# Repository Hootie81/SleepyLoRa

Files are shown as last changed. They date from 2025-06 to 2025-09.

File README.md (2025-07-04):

# SleepyLora Blinds System

A low-power wireless smart blinds system using LoRa to enable low power yet fast response to commands - 100% local control.

In July 2023 I set out the key requirements for the project
- 100% local control - no 3rd party servers etc.
- solar powered with up to 3days bad weather.
- back driveable without breaking.
- secure
- be cheap

This system is 100% local, no external access required at all.

A 2.5w 380mm x 70mm thin film flexible panel is enough to keep a 2000mah battery fully charged with less than 2 hours a day of sun. the 2000mah battery lasts about 10 days with no panel connected.

Key design requirement was for the blinds to still operate by hand, so a mechanism was developed that disengages the motor from the actuator once the move command is complete. [See disengage mechanism video](https://youtu.be/guv8YasCPMQ?si=FenjIrAAZN0NFrJr)

Position is sensed using a linear potentiometer thats connected to the actualing arm, so the blinds always know their position.

The actuators now use a PID controller to target a specified time for each move, this allows the motor to run significantly quieter and allows syncronsation of blinds with different operating forces/friction. All PID, PWM and timing settings are customisable.

All data packets are AES128 encrypted and hardened against replay attacks using 1 second interval TOTP, so no-one can open your blinds but you.
Costs are kept low by using cheap modules form china, assembled onto custom PCB's and housed in 3d printed parts.
The wired slaves are powered by the master, thus only a single battery and solar panel per system and a significant reduction in actuator cost too. 

This project includes electronics designs, firmware, and 3D printable parts for a complete DIY solution.

- [3D Parts Assembly Video](https://youtu.be/qfTnw-1N8DM?si=_8NIrLeuZx0titTB)
- [Electronics Assembly Video](https://youtu.be/dtDF-GL67Ew?si=iw6Ndi3xGu8mUtQ1)

This has been a couple of years in the making, and still very much a work in progress. If you find this project useful, please consider supporting my work:



Your support helps me keep building and maintaining open-source projects like this. Thank you!

---

### System

- **Gateway**:  
  Heltec Wireless Stick Lite V3, Connects to WiFi and MQTT, relays commands between Home Assistant and LoRa network. 
  Exposes a web portal for configuration and security key generation

- **Master**:  
  Blind actuator with a Heltec Wireless Stick Lite V3, voltage booster, motor driver, position sensor and RS485 module.
  Powered from a single cell lipo battery or USB.
  Can supply power to and control multiple slave devices via RS485.
  Exposes a web portal for configuration and firmware updates. (via button press or mqtt command)

- **Slave**:  
  Blind actuator with an ESP32-c3 module, motor driver, position sensor and RS485 module. 
  Powered by the Master
  Exposes a web portal for address configuration and OTA updates. (via button press or mqtt command)
  Connects to the master using a flat 6core telephone cable terminated with 4pin JST XH2.54 connectors
  
---

## Features

- **Long-range LoRa wireless communication**
- **Easy WiFi and MQTT Setup**
- **Easy key generation and sharing**
- **Home Assistant auto-discovery**
- **OTA firmware updates**
- **Configurable RS485 slave addressing**
- **Easy Open/Closed position setting via web portal**
- **PWM speed control with PID controller for quiet operation**
- **Auto calibration feature for disengage mechanism**
- **Low-power operation** 
- **3D-printable hardware** 
- **Easy to assemble electronics**
- **Open-source** 

---

## Project Structure

- **3d_prints/**  
  STL files for all mechanical parts 

- **Electronics/**  
  KiCad schematics, PCB layouts, and Gerber files for the master and slave boards.

- **SleepyLoraGateway/**  
  Firmware for the LoRa gateway device. Handles MQTT, Home Assistant integration, and LoRa communication. 

- **SleepyLoraMaster/**  
  Firmware for the master device, an actuator for one set of shutters, with the capability to power and control several slave devices via RS485.

- **SleepyLoraSlave/**  
  Firmware for the slave device, an actuator for one set of shutters and reports position/status.

---

## Getting Started

- Order all the parts/modules from Aliexpress, list in `Electronics/`
- Order PCB/s using the KiCad files in `Electronics/`
- Print and assemble the required parts from `3d_prints/`
- Solder the modules onto the PCB's
- Install electronics in 3d printed base
- Flash the appropriate firmware to each device:
  - Gateway: `SleepyLoraGateway/`
  - Master: `SleepyLoraMaster/`
  - Slave: `SleepyLoraSlave/`
- Configure the Gateway
  - Connect to the SleepyLoraGateway AP (pw: blind1234)
  - Set the WiFi, MQTT and NTP server information.
  - Set LoRa Region
  - Generate keys and download them. 
  - Save and reboot.
  - Gateway Connects to WiFi, MQTT and Sync's its time.
  - Gateway Publishes gateway metric discovery info and publishes data.
- Configure the Master/s
  - Connect to the SleeplyLoRaMaster AP (pw: blind1234)
  - Load the keys file downloaded above
  - Set Open and Closed limits
  - Save and reboot
  - Master sync's time with gateway
  - Master transmits Device metrics and status to Gateway.
  - Gateway publishes Blind discovery info, subscribes to MQTT topics, and publishes data every 60sec.
  - Master will transmit device metrics and status every minute.
- Check your HA MQTT integration, the Gatway, device and blind will magically appear after a minute or so. 
- Optionally - configure the slave/save
  - Connect the slave to the master 
  - Press the reset button on the master
  - Master will scan for slaves on initial bootup
  - Master transmits slave status to Gateway.
  - Gateway publishes Blind discovery info, subscribes to MQTT topics, and publishes data every 60sec.
  - Open web portal via MQTT or from the master web portal
  - Set Open and Closed limits
  - Master will poll slave and transmit status every minute.
  - Optionally - if a second slave is required
    - press the "Open Web Portal" button on the slave device in HomeAssistant
	- Connect to the SleeplyLoRaSlave AP (pw: blind1234)
	- Change the slave number
	- Save to flash
    - Scan for slaves via the master's web portal (Or press the reset button on the master)
    - Master will rescan for slaves

---

## Documentation

- Each firmware folder contains its own README with build and usage instructions.
- For wiring, assembly, and setup, see my videos on youtube or open an issue for help.

---

## ToDo

- Update slave firmware to use new motor controller library and updated web portal.
- Add feature to get/set all blind settings via MQTT.
- Design an enclosure to the battery and charger modules.
- Make an injection moulding option for the plastic parts.

---

## License

This project is open-source under the MIT License.  
See [LICENSE](LICENSE) for details.

---

## Credits

- Hardware, firmware, and 3D design by Chris Huitema
- Built with [PlatformIO](https://platformio.org/), [KiCad](https://kicad.org/), and [ESPAsyncWebServer](https://github.com/me-no-dev/ESPAsyncWebServer)

---

**Happy hacking and smart shading!**

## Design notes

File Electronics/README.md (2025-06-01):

# Electronics Folder — SleepyLoRa Project

This folder contains all the electronics design files, schematics, PCB layouts, and bills of materials (BOM) for the SleepyLoRa Blinds System. The electronics are designed to be easy to assemble, cost-effective, and reliable for DIY smart blinds control.

## Structure
- **bom.csv** — Common components and extras used across all devices (master, slave, gateway, etc.).
- **Master/** — Schematics, PCB layout, and device-specific BOM for the SleepyLoRaMaster (blind actuator/master controller).
- **Slave/** — Schematics, PCB layout, and device-specific BOM for the SleepyLoRaSlave (slave blind actuator).

Each device folder contains:
- KiCad project files (`.pro`, `.sch`, `.kicad_pcb`, etc.)
- Gerber files for PCB manufacturing
- Device-specific BOM (bill of materials)

## How to Use
1. Review `bom.csv` for the list of common components and extras needed for all devices.
2. For each device (Master, Slave, Gateway):
   - Open the corresponding folder for full schematics, PCB layout, and device-specific BOM.
   - Use the KiCad files to view or modify the design.
   - Use the Gerber files to order PCBs from your preferred manufacturer.
   - Use the device-specific BOM to order parts for that device.
3. Assemble the PCBs according to the schematics and BOMs.

## Notes
- All designs are open-source and provided as-is for DIY use.
- If you make improvements or modifications, please consider contributing back to the project!

## License
SPDX-License-Identifier: MIT

---
For questions or support, open an issue on the main [SleepyLoRa GitHub repository](https://github.com/Hootie81/SleepyLoRa).

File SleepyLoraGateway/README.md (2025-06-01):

# SleepyLoraGateway

SleepyLoraGateway is the gateway firmware for the SleepyLora Blinds System. It acts as a bridge between the local LoRa network of blind actuators and your home automation system (such as Home Assistant) via WiFi and MQTT. The gateway provides secure, local, and reliable communication for smart blind control.

## Features
- Connects to WiFi and MQTT broker for integration with Home Assistant
- Relays commands and status between Home Assistant and LoRa network
- Exposes a web portal for configuration and security key generation
- Handles LoRa communication with master devices
- AES128 encrypted packets with replay protection
- 100% local control, no third-party servers required

## Project Structure
- `src/` — Main source code for the gateway
- `include/` — Shared headers and protocol definitions (e.g., Command_Register.h)
- `lib/` — External and custom libraries
- `platformio.ini` — PlatformIO project configuration

## Getting Started
1. Clone this repository or copy the project to your PlatformIO workspace.
2. Open with VS Code and PlatformIO extension.
3. Connect your gateway hardware (e.g., Heltec Wireless Stick Lite V3).
4. Configure WiFi, MQTT, and LoRa region in the web portal after flashing.
5. Build and upload the firmware using PlatformIO.

## Configuration & Usage
- After flashing, connect to the "SleepyLoraGateway" WiFi AP (password: blind1234).
- Access the web portal to set up WiFi, MQTT, NTP, and LoRa region.
- Generate and download security keys for the system.
- Save and reboot the gateway to connect it to your home network and MQTT broker.
- The gateway will automatically publish device and blind discovery info for Home Assistant.

## Communication Protocol
- **LoRa**: Communicates with master devices using encrypted packets.
- **WiFi/MQTT**: Integrates with Home Assistant and other automation systems.
- **Command Structure**: See `include/Command_Register.h` for command codes and protocol details.

## License
SPDX-License-Identifier: MIT

Copyright (c) 2025 Chris Huitema

---
For more information, see the source code and comments in `src/main.cpp` and related files.

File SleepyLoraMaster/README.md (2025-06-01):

# SleepyLoRaMaster

SleepyLoRaMaster is the firmware for the Master actuator device
  The Master actuator device is a plantation shutter blind actuator with a 
  Heltec Wireless Stick Lite V3, voltage booster, motor driver, position sensor and RS485 module.
  Powered from a single cell lipo battery or USB.
  Can supply power to and control multiple slave devices via RS485.
  Exposes a web portal for configuration and firmware updates. (via button press or mqtt command)

## Project Structure
- `src/` — Main source code for the master controller
- `include/` — Shared headers and protocol definitions (e.g., Command_Register.h)
- `lib/` — External and custom libraries
- `platformio.ini` — PlatformIO project configuration

## Getting Started
1. Clone this repository or copy the project to your PlatformIO workspace.
2. Open with VS Code and PlatformIO extension.
3. Connect your master controller hardware (e.g., ESP32 or compatible MCU).
4. Configure any hardware-specific settings in `platformio.ini` or source files as needed.
5. Build and upload the firmware using PlatformIO.

## Communication Protocol
- **RS485 UART**: Used to communicate with slave devices. Each slave has a unique address.
- **LoRa**: Used for long-range wireless communication with a gateway using a custom encrypted protocol.

## License
SPDX-License-Identifier: MIT

Copyright (c) 2025 Chris Huitema

---
For more information, see the source code and comments in `src/main.cpp` and related files.

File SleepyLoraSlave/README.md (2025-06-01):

# SleepyLoraSlave

SleepyLoraSlave is the firmware for the slave blind actuator in the SleepyLora Blinds System. It receives commands from the master controller via RS485 UART, controls a blind motor, and reports its position and state back to the master. The slave can be configured and updated via a built-in web portal.

## Features
- Receives commands from the master controller over RS485 UART
- Controls a blind motor and reports position/state
- Web portal for configuration (slave address, etc.)
- OTA firmware updates via web portal
- Powered by the master device
- Low-power operation

## Project Structure
- `src/` — Main source code for the slave controller
- `include/` — Shared headers and protocol definitions
- `lib/` — External and custom libraries
- `platformio.ini` — PlatformIO project configuration

## Getting Started
1. Clone this repository or copy the project to your PlatformIO workspace.
2. Open with VS Code and PlatformIO extension.
3. Connect your slave hardware (e.g., ESP32-C3 or compatible MCU).
4. Configure any hardware-specific settings in `platformio.ini` or source files as needed.
5. Build and upload the firmware using PlatformIO.

## Configuration & Usage
- Connect the slave to the master using a flat 6-core telephone cable (terminated with 4-pin JST XH2.54 connectors).
- To configure the slave address or update firmware:
  - Press the button to activate the web portal.
  - Connect to the "SleepyLoRaSlave" WiFi AP (password: blind1234).
  - Access the configuration page to set the slave number or upload new firmware.

## Communication Protocol
- **RS485 UART**: Used to communicate with the master device. Each slave has a unique address.
- **Command Structure**: See `include/Command_Register.h` for command codes and protocol details.

## License
SPDX-License-Identifier: MIT

Copyright (c) 2025 Chris Huitema

---
For more information, see the source code and comments in `src/main.cpp` and related files.

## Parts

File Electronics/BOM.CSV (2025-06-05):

Part No | qty | link | notes
GA12-N20 DC 3V 6V 12V Micro Metal Gear Motor Gear Wheel Gear Motor 30RPM | 1 | https://www.aliexpress.com/item/1005005699205905.html | 3v 30rpm version
Metal Dowel Pins Stainless Steel M1 x 10mm Cylindrical Pin Locating Dowel Parallel Pins Solid Rod | 2 | https://www.aliexpress.com/item/1005005478162210.html | M1 x 10
Metal Dowel Pins Stainless Steel M2 x 20mm Cylindrical Pin Locating Dowel Parallel Pins Solid Rod | 2 | https://www.aliexpress.com/item/1005005478162210.html | M2 x 20
Hexagon Hex Socket Countersunk Flat Head Screw M3 x 6mm DIN7991 304 Stainless Steel | 2 | https://www.aliexpress.com/item/1005006180128211.html | M3 x 6
M2 Micro Carbon Steel Cross Phillips Flat Countersunk Self Tapping Screw Machine Laptop Screws | 2 | https://www.aliexpress.com/item/1005004177352184.html | M2 x 16
JST XH2.54 Metal Pin | 2 | https://www.aliexpress.com/item/1005003422202370.html
JST XH2.54 4 Pin Terminals Plastic Female Socket Wire Connector XH 2.54 4P | 1 | https://www.aliexpress.com/item/1005003422202370.html
M2 Micro Carbon Steel Cross Phillips Flat Countersunk Self Tapping Screw Machine Laptop Screws | 3 | https://www.aliexpress.com/item/1005004177352184.html | M2 x 5
M2 Micro Carbon Steel Cross Phillips Flat Countersunk Self Tapping Screw Machine Laptop Screws | 1 | https://www.aliexpress.com/item/1005004177352184.html | M2 x 12
For Slave Cables:
Flat electrical wire 20251 28AWG 6Core Black/White PVC sheath flat cable wire for RJ12 6P6C telephone Cable | x | https://www.aliexpress.com/item/1005006661746215.html
Super Thin High Temperature Resistant Double Sided Adhesive Tape For TV Backlight Article Lamp 5mm/8mm | x | https://www.aliexpress.com/item/33004448687.html
JST XH2.54 Metal Pin | 8 | https://www.aliexpress.com/item/1005003422202370.html
JST XH2.54 4 Pin Terminals Plastic Female Socket Wire Connector XH 2.54 4P | 2 | https://www.aliexpress.com/item/1005003422202370.html
For Solar Charger:
PCM BMS Li-ion Li-polymer 1S 3.6V 3.7V 1S 18650 21700 Lithium Battery PCB Protection Board 1.5A 2A 3A 3.5A 5A Charge Discharge |  | https://www.aliexpress.com/item/1005006052849266.html
1 Cell Lithium Battery Charging 3.7V 4.2V CN3791 MPPT Solar Panel Regulator Controller Module 5V 6V 9V 12V |  | https://www.aliexpress.com/item/1005007355378997.html
18V 3.8W 236mA Mini Solar Panel 470X60MM Solar Cell DIY For Light Cell Phone Toys Chargers Portable TZT High Quality |  | https://www.aliexpress.com/item/1005008600638476.html
5Pcs SH1.0 JST1.25 ZH1.5 To PH2.0 To XH2.54 Adapter Conversion Terminal Wire Connecting Line Cable 2P 3P 4P 5P 6P |  | https://www.aliexpress.com/item/1005006895796837.html | 1.25 to PH2.0 2P 20CM Same direction
Recommended tools:
Micro Connector Crimping Tool YE-013BR For XH2.54/PH2.0/ZH1.5 D-Sub Open Barrel Suits Molex JST Pliers 0.03-0.5mm²/32-20AWG |  |  | https://www.aliexpress.com/item/1005005953582688.html
80 Gears Spot Welder Adjustable Portable Handheld Digital Display Mini Spot Welding Machine Automatic Trigger for 18650 Battery |  | https://www.aliexpress.com/item/1005005611551469.html

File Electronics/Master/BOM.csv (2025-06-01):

ID | Part No | qty | link | notes
U1 | DRV8833 module | 1 | https://www.aliexpress.com/item/1005007347094702.html | 6pins each side not 7
U2 | Heltec Wireless stick lite v3 | 1 | https://www.aliexpress.com/item/1005005164155546.html | Ensure correct frequency for your area
 | 915MHz FPC Antenna PCB Anteana | 1 | https://www.aliexpress.com/item/1005006958686850.html | 5mm x 75mm version
U3 | Mini DC Boost Converter Board 3.7V to 12V Step Up Board Voltage Regulator PCB Board Electronic Voltage Module | 1 | https://www.aliexpress.com/item/1005006115043704.html | set to 5v output
U4 | MAX3485 unidirection module 3.3v version | 1 | https://www.aliexpress.com/item/1005006186051306.html | 5pins 1 side, 3 on other
R1 | 10k 1/4w resistor | 1
SW1 | Middle 2Pin 6x6x6mm Switch Tactile Push Button | 1 | https://www.aliexpress.com/item/1005005917191424.html
RV1 | 128mm B10K Single Channel Sliding Potentiometer Stroke 100mm Handle 8mm | 1 | https://www.aliexpress.com/item/1005005470862119.html
J1, J2, J3 | JST XH2.54 4 Pin Terminals Plastic Shell Male Plug | 3 | https://www.aliexpress.com/item/1005003422202370.html
C1, C2 | 100nf Ceramic cap 50v 0.1uf | 2 | https://www.aliexpress.com/item/32971478818.html

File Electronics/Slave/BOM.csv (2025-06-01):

ID | Part No | qty | link | notes
U1 | DRV8833 module | 1 | https://www.aliexpress.com/item/1005007347094702.html | 6pins each side not 7
U2 | ESP32 SuperMini Development Board ESP32-C3 Development Board | 1 | https://www.aliexpress.com/item/1005006350465839.html
U3 | MAX3485 unidirection module 3.3v version | 1 | https://www.aliexpress.com/item/1005006186051306.html | 5pins 1 side, 3 on other
R1,R2, R3, R4, R5, R6 | 10k 1/4w resistor | 6 |  | 1required, 2-6 optional
RV1 | 128mm B10K Single Channel Sliding Potentiometer Stroke 100mm Handle 8mm | 1 | https://www.aliexpress.com/item/1005005470862119.html
J1, J2, J3 | JST XH2.54 4 Pin Terminals Plastic Shell Male Plug | 3 | https://www.aliexpress.com/item/1005003422202370.html
C1, C2, C3, C4 | 100nf Ceramic cap 50v 0.1uf | 3 | https://www.aliexpress.com/item/32971478818.html

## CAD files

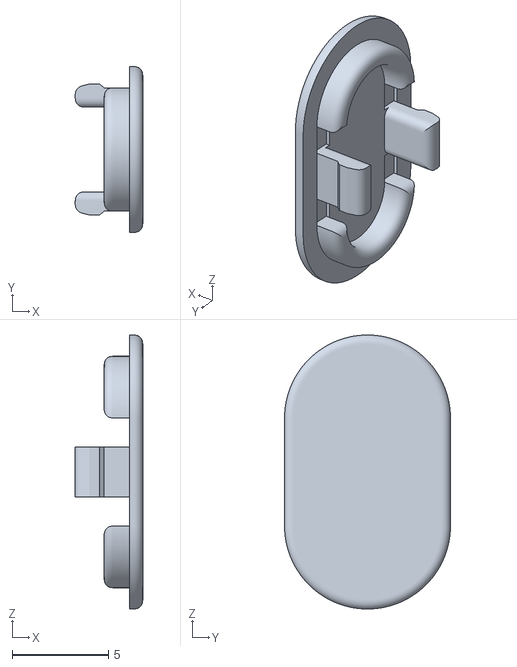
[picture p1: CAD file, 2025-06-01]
3d_prints/USB cover.stl
3.50 x 8.60 x 14.2

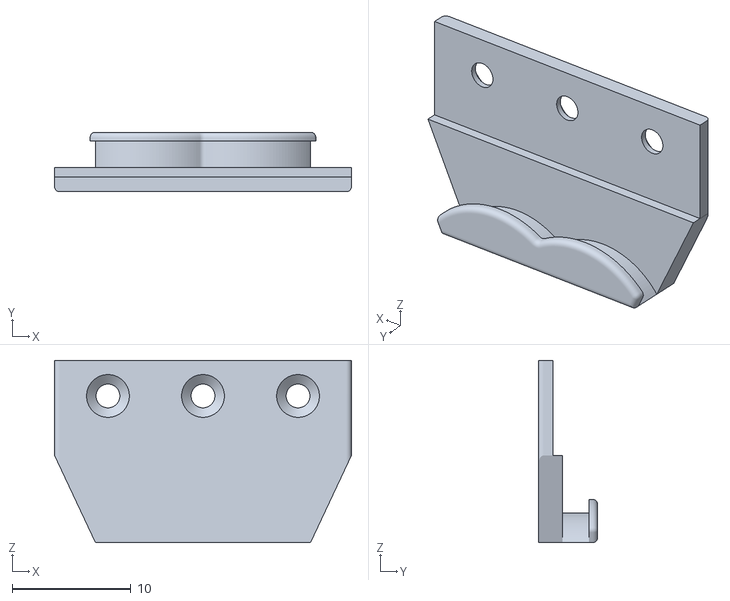
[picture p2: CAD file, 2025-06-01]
3d_prints/Clamp Style A.stl
25.0 x 5.00 x 15.4

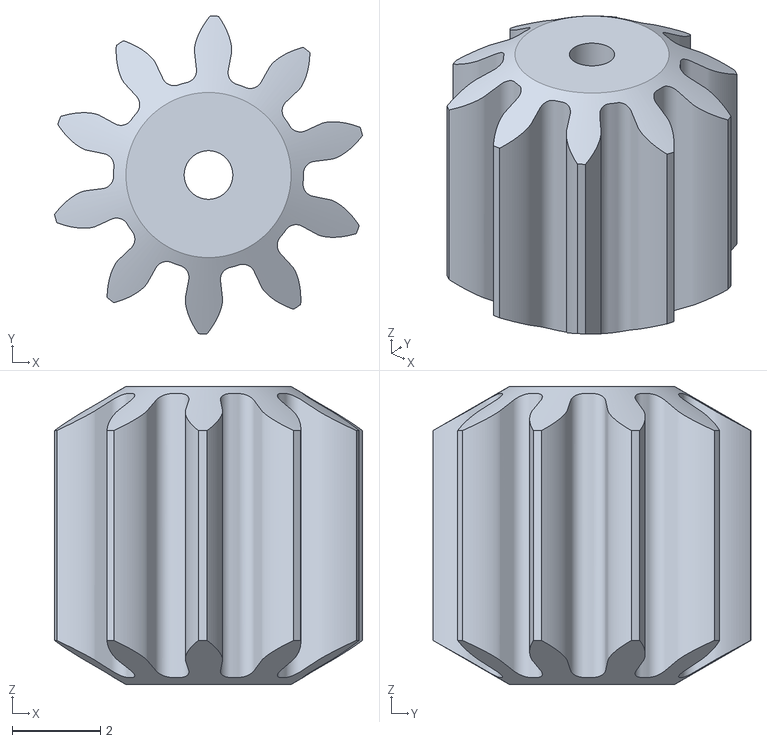
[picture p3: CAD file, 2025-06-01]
3d_prints/Spur gear 10 teeth A.stl
6.97 x 7.20 x 6.75

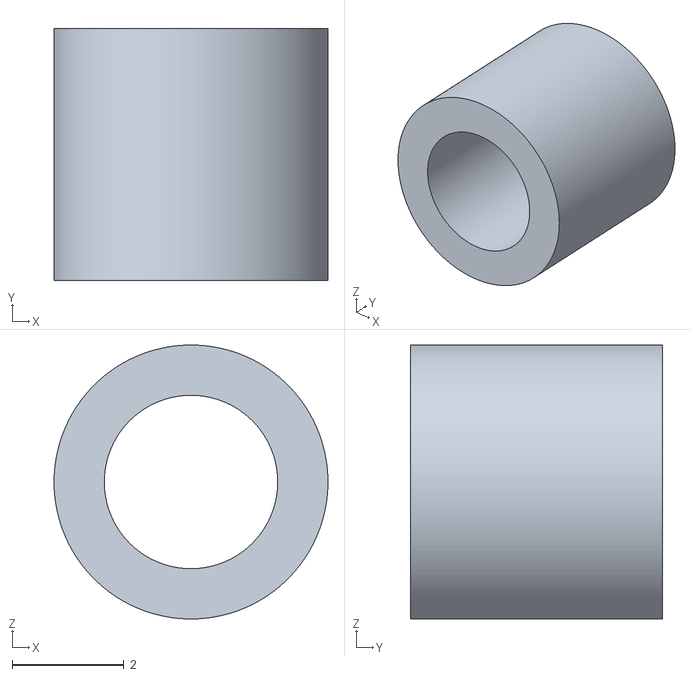
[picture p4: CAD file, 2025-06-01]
3d_prints/bearing.stl
4.90 x 4.50 x 4.90

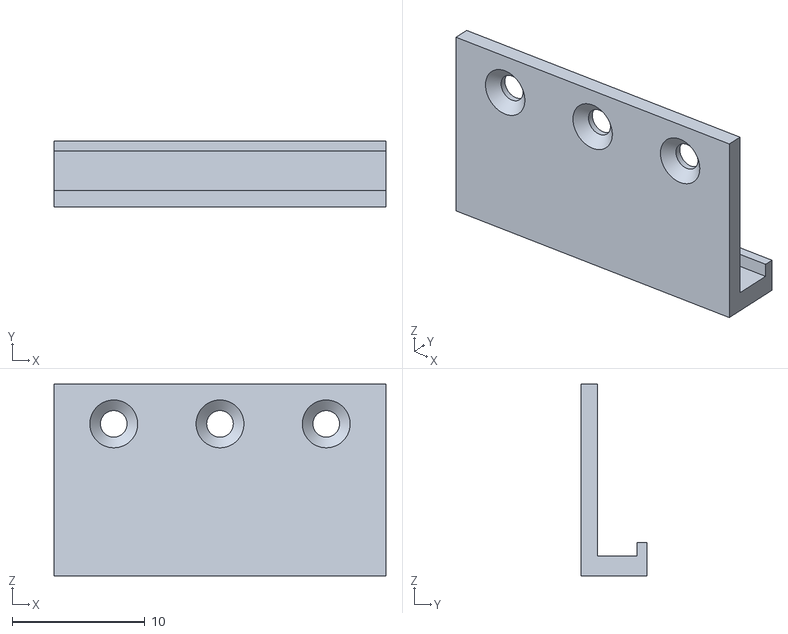
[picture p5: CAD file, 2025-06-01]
3d_prints/Clamp Style B.stl
25.0 x 5.00 x 14.5

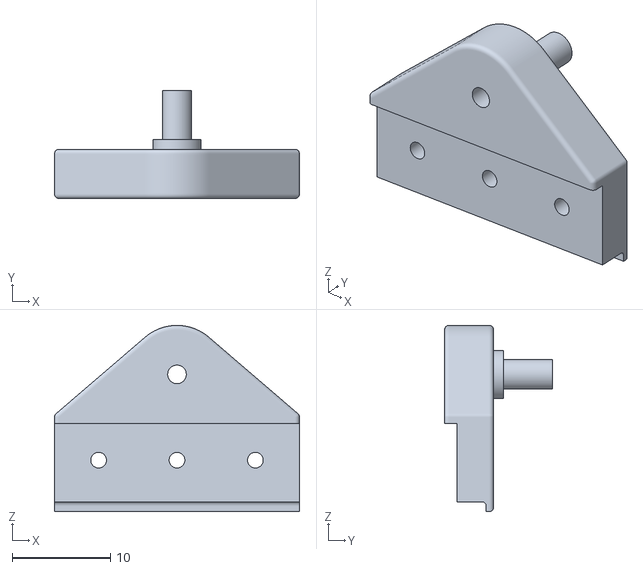
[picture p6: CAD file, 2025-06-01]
3d_prints/Clamp 1.stl
25.0 x 11.0 x 19.0

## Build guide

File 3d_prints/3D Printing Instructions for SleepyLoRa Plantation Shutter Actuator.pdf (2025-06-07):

# 3D Printing Instructions for SleepyLoRa Plantation Shutter Actuator

Comprehensive Guidelines for Printing and Cleaning

## Overview

The SleepyLoRa plantation shutter actuator is designed to be easy to print and assemble. Over a dozen prototypes have led to this design, with just enough space to fit the necessary components and to tidy excess cable inside. This guide provides step-by-step instructions for 3D printing its parts, using the recommended resin type, ensuring proper cleaning and safety practices. The files for this project are hosted on GitHub here
https://github.com/Hootie81/SleepyLoRa/tree/main/3d_prints STL’s for all the parts are available, and pre-supported files for Chitubox, in an array of 6 for the large pieces, and an array of 4 for the smaller parts. There is a left and right variation of the actuator arm

## Required Materials and Equipment

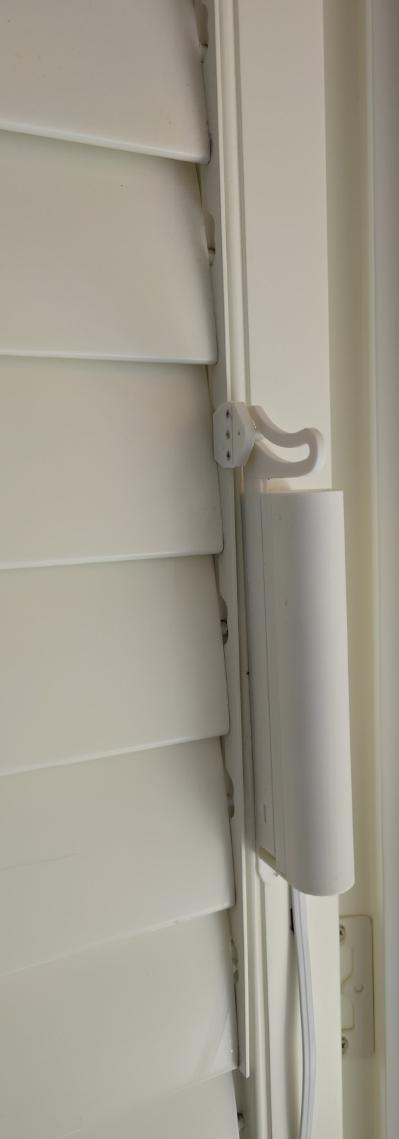
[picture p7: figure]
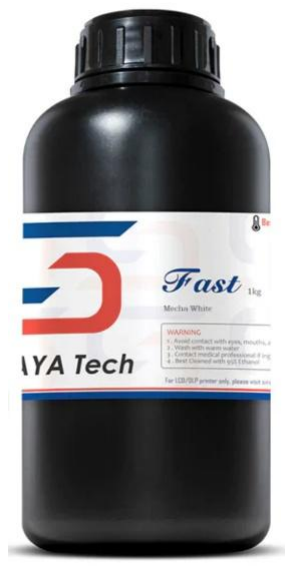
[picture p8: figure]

- Resin: Siraya Tech Fast Mecha White – This resin has been tested and proven to possess the optimal properties for the actuator's tight tolerances. https://siraya.tech/products/siraya-tech-fast-abs-like-wearresistant-resin?variant=41963498504301 (https://siraya.tech/products/siraya-tech-fast-abs-like-wear-resistant-resin?variant=41963498504301)
- Alternative resin for internals – Siraya Tech Build Sonic Grey, perfect low shrinkage and non-brittle for the internal components. And its much cheaper than the mecha white. Shame its not white! https://siraya.tech/products/buildresin-drillable-precision-printing?variant=40152208212077 (https://siraya.tech/products/build-resin-drillable-precision-printing?variant=40152208212077)

- 3D Printer: Ensure your printer has a build height of at least 190mm for the large parts, the small parts will fit on most printers. I use an Anycubic Photon mono for the internals and a Creality Halot Mage for the large parts.
- Heater for printer if printing below 25°C, as the tall print takes
over 20hours to print I highly recommend spending the
money, I found the parts get thicker when its cold and don’t fit https://www.aliexpress.com/item/1005006860975250.html
- Cleaning Supplies:
- Isopropyl alcohol (IPA) or resin cleaner
- Three containers for the rinse process
- Air compressor or high-power blower
- Nitrile gloves
- Paper towels or lint-free cloths

## Safety Instructions

- Protective Equipment:
- Safety goggles,
- nitrile gloves
- well-ventilated workspace or a respirator if necessary.

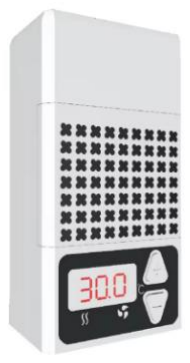
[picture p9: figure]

- Ensure a bin is nearby for putting waste resin/build supports, dirty rags etc.
Resin can make a mess, I print in the carport for ventilation and in case I make mistakes. I have had resin vats fail and leak everywhere. Always wear eye protection, parts snap easily and resin has a magnetic attraction to your eyes, especially when removing supports and cleaning.

## 3D Printing Instructions

## Step 1: File Setup

1. Download the STL files from the GitHub repository https://github.com/Hootie81/SleepyLoRa/tree/main/3d_prints and import them into your preferred slicing software. I prefer Chitubox pro, the extra features have been useful
2. Configure the slicing settings for the Sirayatech Fast Mecha White resin. Recommended settings include:
- Layer height: 50 microns
- Exposure time: 1.7s
- Tolerance Compensation: a: -0.070 b: -0.070
- Supports: Add sufficient supports, particularly for overhangs. Think about pulling force directions when the print is lifting, ensure there is support directly below
where its pulling from otherwise the part will end up like
a banana. I use light support and lots of it.

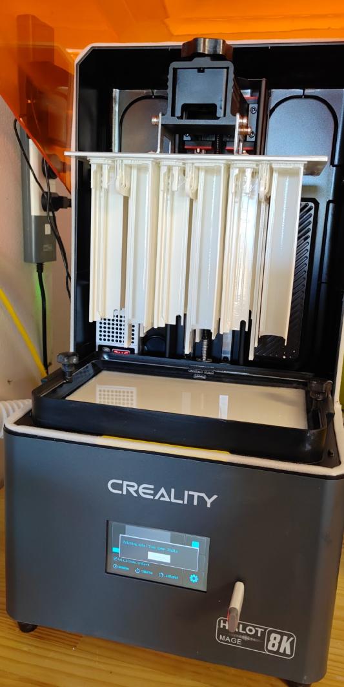
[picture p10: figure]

3. Ensure the model's orientation minimizes the need for excessive supports and allows for proper drainage. For the long parts I print them completely vertical, this minimises warping.

## Step 2: Printer Preparation

1. Ensure your 3D printer has been levelled as per the manufacturer’s instructions.
2. Thoroughly mix and pour the Siraya tech Fast Mecha White resin into the printer's vat.
3. Turn on the heater, I run mine at 30°C
3. Perform test prints to ensure the exposure time and tolerance compensation are set correctly. With Mecha White I found a resin exposure of 1.7sec and a tolerance compensation of -0.07 for both internal and external surfaces gave me best results. I use the same settings on the Anycubic Photon Mono and Halot Mage. The settings on the Siraya Tech website don’t give good results
4. Double check the bottom of your resin vat for any lumps!

## Step 3: Printing

1. Start the 3D printing process.
2. Monitor the initial layers to ensure proper adhesion to the build platform.
3. Wait the 20 odd hours to print

## Post-Processing and Cleaning

## Safety Precautions

1. Always wear nitrile gloves and safety goggles when handling uncured resin.
2. Work in a well-ventilated area to avoid inhaling fumes.
3. Avoid direct skin contact with resin and clean any spills immediately.

## Cleaning the Printed Parts

The cleaning process is critical for ensuring the actuator parts achieve the necessary tolerances and functionality. Follow these steps meticulously:
Note: don’t perform trial fit until after the curing process is complete, trust me!
Step 1: Separate parts from support
material
1. Separate the support material from the
parts. Most parts can be removed while on the build plate. A small mason jar or a tea strainer will be useful for the gears
and small parts. Don’t waste alcohol
cleaning up the support material, remove

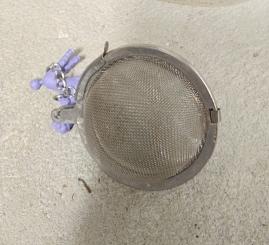
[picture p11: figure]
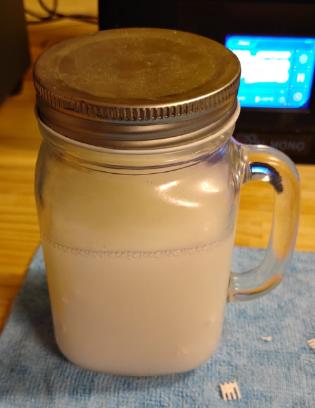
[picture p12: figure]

the parts and put the support material in the sun for a few hours to cure and bin it.
Step 1: Initial Rinse
1. In small batches submerge the printed parts in the first container filled with isopropyl alcohol (IPA) or resin cleaner.
2. Gently agitate the part for approximately 30 seconds to remove excess resin.
Step 2: Second Rinse
1. Transfer the part to a second container filled with clean IPA.
2. Repeat the agitation process for another 2-3 minutes to further remove resin residues.
Step 3: Final Rinse
1. Move the part to a third container with fresh IPA for the final cleaning step.
2. Agitate the part again for 2-3 minutes to ensure all traces of resin are removed.

Step 4: Blow Dry
1. Use compressed air to thoroughly dry the part, paying particular attention to the profiles where the cover slides onto the base, the antenna slot and the actuator teeth, and gears. This step is crucial due to the actuator's tight tolerances. Leaving the alcohol to evaporate will leave residue on the part.
2. Inspect all the gear profiles for support material, the supports are the exact size to fit in the gears they tend to stick really well in there.

## Curing the Parts

1. Place the cleaned parts in a UV curing chamber or under a UV lamp.
2. Follow the resin manufacturer’s recommended curing times to achieve full mechanical properties. I typically do 6 minutes
3. a foam block with slots cut helps to cure the long actuator arms.

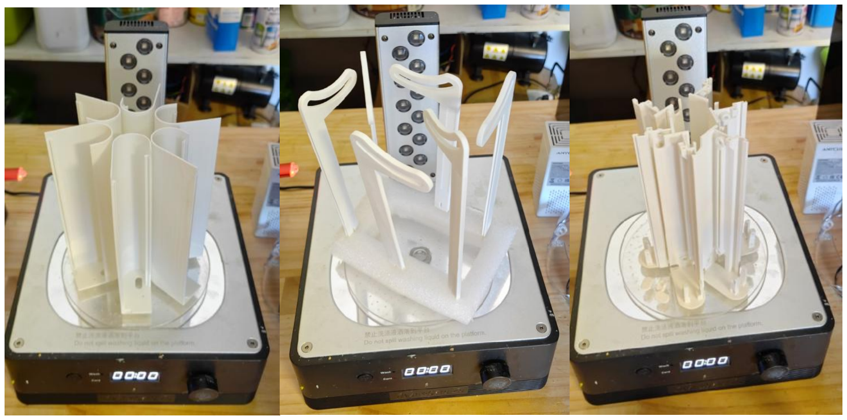
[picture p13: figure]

## Assembly and Testing

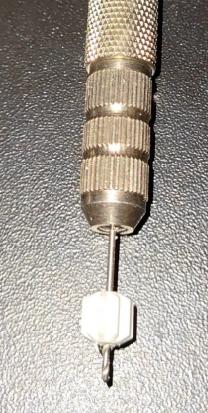
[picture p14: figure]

1. Once the parts are fully cured, carefully inspect them for any defects or resin residues.
2. Use a 1mm drill bit to clean the holes in the small gears, file any remaining support material off, and ensure the inside of the cam profile is smooth.
2. Assemble the parts, how to video here https://youtu.be/qfTnw-1N8DM?si=aZ-7PTGw5bI3fyB_

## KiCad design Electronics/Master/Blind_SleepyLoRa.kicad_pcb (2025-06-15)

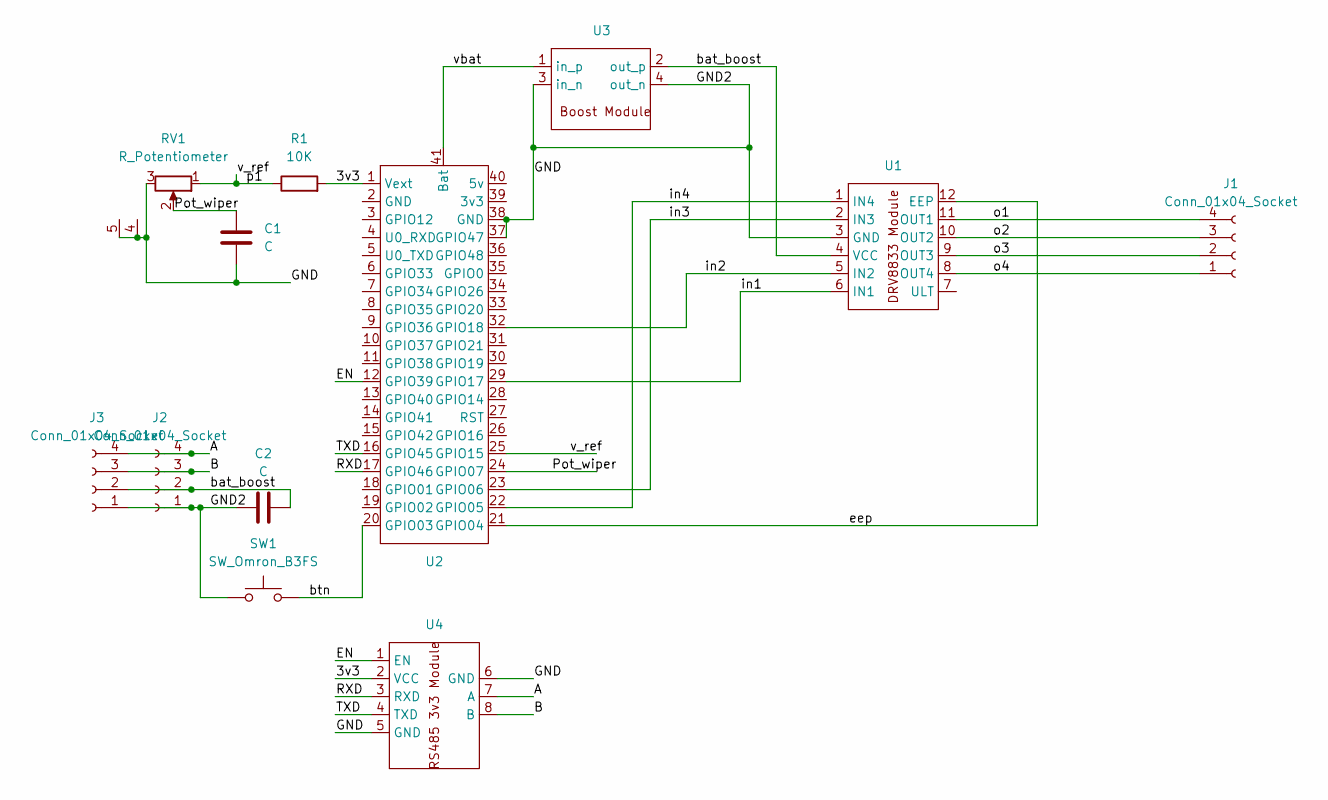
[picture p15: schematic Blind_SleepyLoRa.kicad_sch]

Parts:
C1, C2: C; C_Disc_D5.0mm_W2.5mm_P5.00mm
J1: Conn_01x04_Socket; JST_XH_B4B-XH-AM_1x04_P2.50mm_Vertical
J2, J3: Conn_01x04_Socket; JST_XH_B4B-XH-A_1x04_P2.50mm_Vertical
R1: 10K; R_Axial_DIN0309_L9.0mm_D3.2mm_P12.70mm_Horizontal
RV1: R_Potentiometer; linear_pot_128mm
SW1: SW_Omron_B3FS; SW_PUSH_6mm_H4.3mm
U1: drv8833_module
U2: WSL
U3: Boost_module
U4: RS485_3v3_module

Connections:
/3v3: R1.2, U2.1 (Vext), U4.2 (VCC)
/A: J2.4, J3.4, U4.7 (A)
/B: J2.3, J3.3, U4.8 (B)
/EN: U2.12 (GPIO39), U4.1 (EN)
/GND: C1.2, C2.2, J2.1, J3.1, RV1.3, RV1.4 (shld), RV1.5 (shld), SW1.1, U1.3 (GND), U2.37 (GPIO47), U2.38 (GND), U3.3 (in_n), U3.4 (out_n), U4.5 (GND), U4.6 (GND)
/Pot_wiper: C1.1, RV1.2, U2.24 (GPIO07)
/RXD: U2.17 (GPIO46), U4.3 (RXD)
/TXD: U2.16 (GPIO45), U4.4 (TXD)
/bat_boost: C2.1, J2.2, J3.2, U1.4 (VCC), U3.2 (out_p)
/btn: SW1.2, U2.20 (GPIO03)
/eep: U1.12 (EEP), U2.21 (GPIO04)
/in1: U1.6 (IN1), U2.29 (GPIO17)
/in2: U1.5 (IN2), U2.32 (GPIO18)
/in3: U1.2 (IN3), U2.23 (GPIO06)
/in4: U1.1 (IN4), U2.22 (GPIO05)
/o1: J1.4, U1.11 (OUT1)
/o2: J1.3, U1.10 (OUT2)
/o3: J1.2, U1.9 (OUT3)
/o4: J1.1, U1.8 (OUT4)
/p1: R1.1, RV1.1, U2.25 (GPIO15)
/vbat: U2.41 (Bat), U3.1 (in_p)

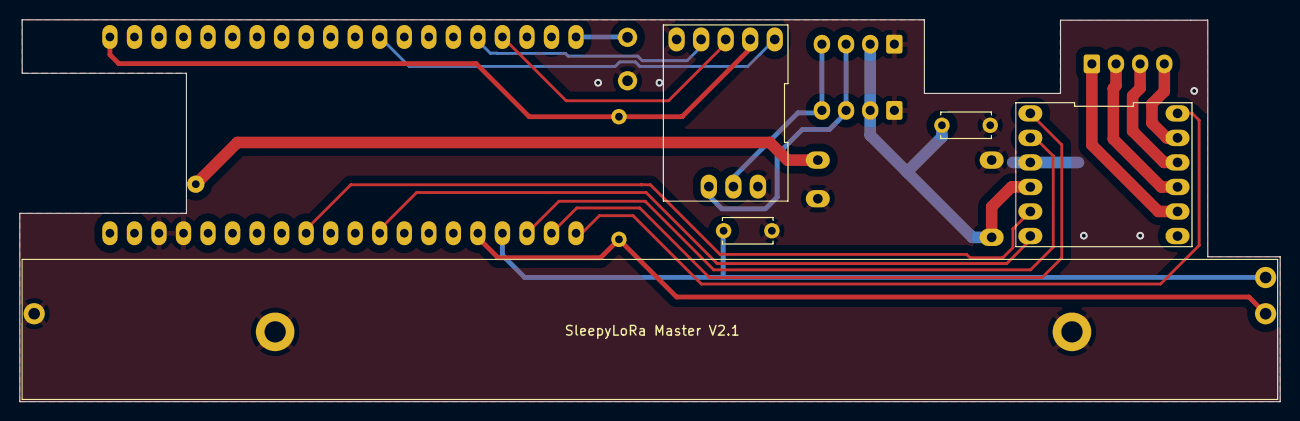
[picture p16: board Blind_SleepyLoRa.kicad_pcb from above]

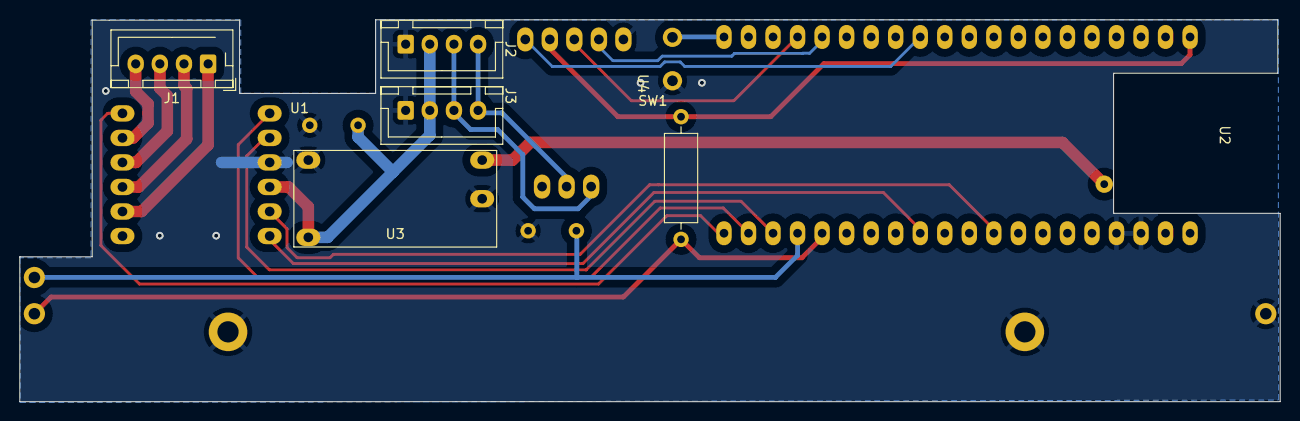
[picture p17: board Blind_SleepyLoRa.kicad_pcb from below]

Board: 2 copper layers, 130.5 x 39.5 mm, 12 parts (7 on the bottom side), 21 nets.

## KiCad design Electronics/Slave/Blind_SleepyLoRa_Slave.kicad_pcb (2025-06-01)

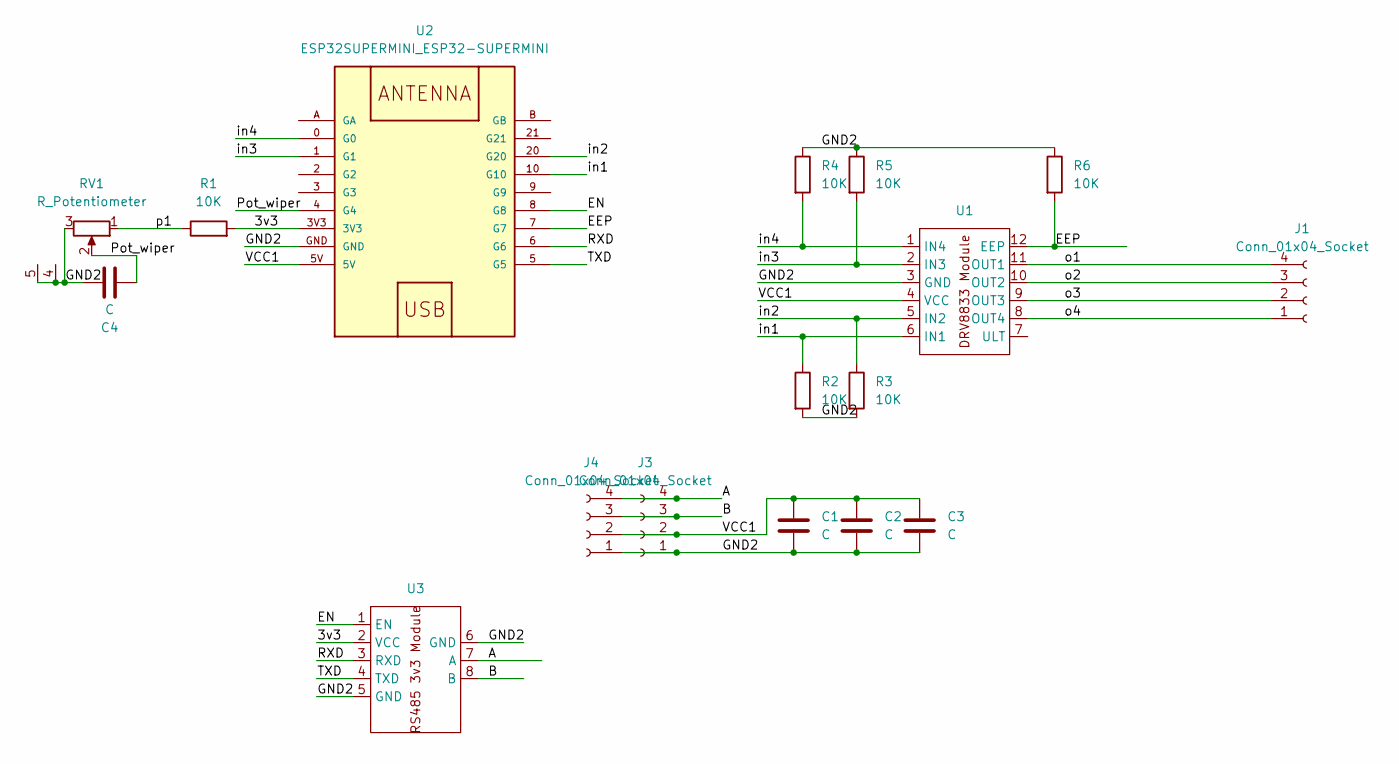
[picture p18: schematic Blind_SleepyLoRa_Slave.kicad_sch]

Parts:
C1, C2, C3, C4: C; C_Disc_D5.0mm_W2.5mm_P5.00mm
J1: Conn_01x04_Socket; JST_XH_B4B-XH-AM_1x04_P2.50mm_Vertical
J3, J4: Conn_01x04_Socket; JST_XH_B4B-XH-A_1x04_P2.50mm_Vertical
R1, R2, R3, R4, R5, R6: 10K; R_Axial_DIN0309_L9.0mm_D3.2mm_P12.70mm_Horizontal
RV1: R_Potentiometer; linear_pot_128mm
U1: drv8833_module
U2: ESP32SUPERMINI_ESP32-SUPERMINI
U3: RS485_3v3_module

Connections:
/3v3: R1.2, U2.3V3, U3.2 (VCC)
/A: J3.4, J4.4, U3.7 (A)
/B: J3.3, J4.3, U3.8 (B)
/EEP: R6.2, U1.12 (EEP), U2.7 (G7)
/EN: U2.8 (G8), U3.1 (EN)
/GND2: C1.2, C2.2, C3.2, C4.2, J3.1, J4.1, R2.2, R3.2, R4.1, R5.1, R6.1, RV1.3, RV1.4 (shld), RV1.5 (shld), U1.3 (GND), U2.GND, U3.5 (GND), U3.6 (GND)
/Pot_wiper: C4.1, RV1.2, U2.4 (G4)
/RXD: U2.6 (G6), U3.3 (RXD)
/TXD: U2.5 (G5), U3.4 (TXD)
/VCC1: C1.1, C2.1, C3.1, J3.2, J4.2, U1.4 (VCC), U2.5V
/in1: R2.1, U1.6 (IN1), U2.10 (G10)
/in2: R3.1, U1.5 (IN2), U2.20 (G20)
/in3: R5.2, U1.2 (IN3), U2.1 (G1)
/in4: R4.2, U1.1 (IN4), U2.0 (G0)
/o1: J1.4, U1.11 (OUT1)
/o2: J1.3, U1.10 (OUT2)
/o3: J1.2, U1.9 (OUT3)
/o4: J1.1, U1.8 (OUT4)
/p1: R1.1, RV1.1

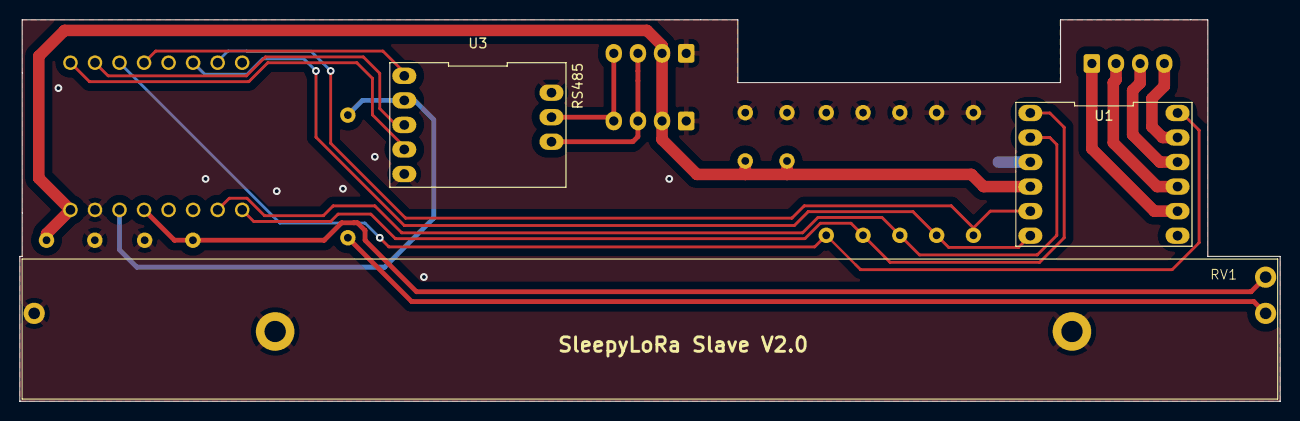
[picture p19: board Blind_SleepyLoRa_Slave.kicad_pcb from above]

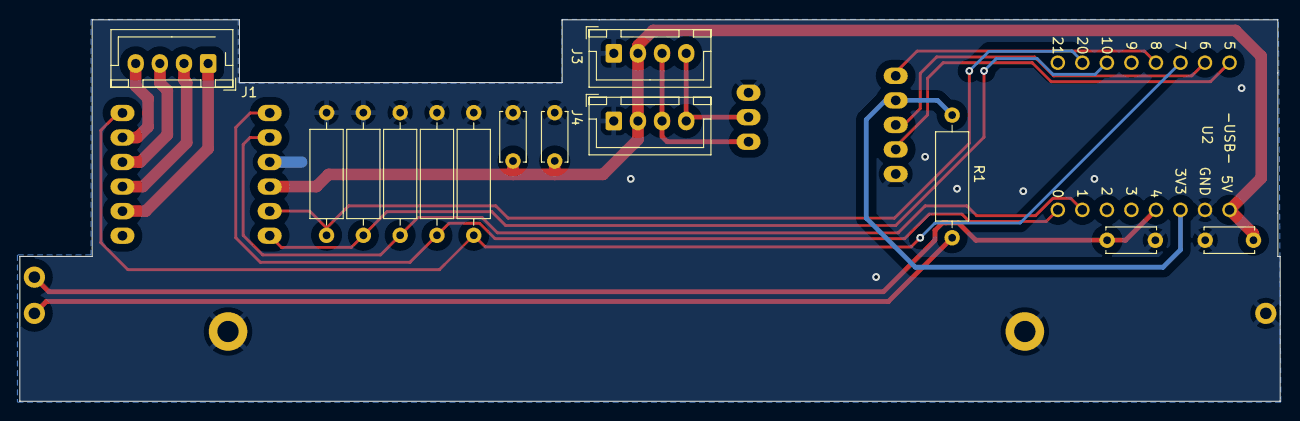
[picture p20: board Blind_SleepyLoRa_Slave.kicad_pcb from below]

Board: 2 copper layers, 130.5 x 39.5 mm, 17 parts (14 on the bottom side), 19 nets.

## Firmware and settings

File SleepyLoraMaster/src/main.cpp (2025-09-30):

// SPDX-License-Identifier: MIT
// Copyright (c) 2025 Chris Huitema

// SleepyLoRaMaster blind controller firmware. Receives commands via LoRa from the Gateway.
// This Master device controls a blind motor and reports its position and state back to the Gateway.
// The master controller is responsible for managing the LoRa communication and forwarding commands to slave devices via RS485.
// The master controller can also be configured via a web portal to change its settings.
// The device can be updated OTA via the web portal.
// the master will scan for RS485 slaves on startup and store them in flash.
// The master will also periodically check the status of the slaves and update the Gateway with their information.
// The master will also handle any incoming commands from the Gateway and forward them to the appropriate slave device.


#include <Arduino.h>
#include <SX126x-Arduino.h>
#include <SPI.h>
#include <Ticker.h>
#include <rom/rtc.h>
#include <driver/rtc_io.h>
#include <ESP32Time.h>
#include <CryptoAES_CBC.h> /* https://github.com/Obsttube/CryptoAES_CBC/tree/master */
#include <AES.h>           /* https://github.com/Obsttube/CryptoAES_CBC/tree/master */
#include <string.h>        /* https://github.com/Obsttube/CryptoAES_CBC/tree/master */
#include "sha1.h"          // for OTP
#include "TOTP.h"          // for OTP
#include <Ewma.h>          // exponential weighted moving average for position and batt voltage filtering
#include <Preferences.h>
#include <ArduinoJson.h>
#include <Wire.h> // I2C master
#include <nvs_flash.h>
#include <AsyncEventSource.h>
#include <algorithm> // For std::min and std::max

#include "LoRa_settings.h"
#include "Device_settings.h"
#include "Command_Register.h"

#define CIRCULAR_BUFFER_INT_SAFE
#include "CircularBuffer.h"

#include <WiFi.h>
#include <AsyncTCP.h>
#include <ESPAsyncWebServer.h>
#include <vector>
#include <Update.h>

#include <BlindMotorController.h>
#include "web_portal.h"

// Debug macros with log levels
#define DEBUG_SERIAL

#define LOG_LEVEL_ERROR   1
#define LOG_LEVEL_WARN    2
#define LOG_LEVEL_INFO    3
#define LOG_LEVEL_DEBUG   4

#ifndef DEBUG_LEVEL
#define DEBUG_LEVEL LOG_LEVEL_DEBUG  // Set default log level here
#endif

#ifdef DEBUG_SERIAL
  #define LOG_ERROR(...)   do { if (DEBUG_LEVEL >= LOG_LEVEL_ERROR) Serial.printf("[ERROR] " __VA_ARGS__); } while(0)
  #define LOG_WARN(...)    do { if (DEBUG_LEVEL >= LOG_LEVEL_WARN)  Serial.printf("[WARN] "  __VA_ARGS__); } while(0)
  #define LOG_INFO(...)    do { if (DEBUG_LEVEL >= LOG_LEVEL_INFO)  Serial.printf("[INFO] "  __VA_ARGS__); } while(0)
  #define LOG_INFO_RAW(...) do { if (DEBUG_LEVEL >= LOG_LEVEL_INFO)  Serial.printf(__VA_ARGS__); } while(0)
  #define LOG_DEBUG(...)   do { if (DEBUG_LEVEL >= LOG_LEVEL_DEBUG) Serial.printf("[DEBUG] " __VA_ARGS__); } while(0)
  #define LOG_DEBUG_RAW(...) do { if (DEBUG_LEVEL >= LOG_LEVEL_DEBUG) Serial.printf(__VA_ARGS__); } while(0)
#else
  #define LOG_ERROR(...)
  #define LOG_WARN(...)
  #define LOG_INFO(...)
  #define LOG_INFO_RAW(...)
  #define LOG_DEBUG(...)
  #define LOG_DEBUG_RAW(...)
#endif



// Set to 1 to stop any output on Serial
#define BATT_SAVE_ON 0

#define CONFIG_BTN_INPUT 40
#define CONFIG_BTN_OUTPUT 42

#define DEBOUNCE_MS 50
#define LONG_PRESS_MS 2000

#define BASE_ADDR 0x20 // Example base address for slaves
#define MAX_SLAVES 12    // Adjust as needed

// UART protocol constants
#define RS485_DIR_PIN 39
#define UART_TX_PIN     46
#define UART_RX_PIN      45
#define RS485_TRANSMIT()  digitalWrite(RS485_DIR_PIN, HIGH)
#define RS485_RECEIVE()   digitalWrite(RS485_DIR_PIN, LOW)
#define UART_START_BYTE 0xAA
#define UART_END_BYTE   0x55
#define UART_BAUDRATE   115200

// dummy values for common library
uint8_t slave_number = 0;
uint8_t rs485_addr = 0;
bool isAddressInUse(unsigned char) { return false; }

#define GET_STATUS 0x08
#define UPDATE_SLAVE 0x09
#define UART_TIMEOUT_MS 90
#define BLIND_COMMAND 0x03

uint8_t slave_miss_count[MAX_SLAVES+1] = {0}; // Track missed polls per slave
#define SLAVE_MISS_THRESHOLD 3                // Number of missed polls before marking as not moving

int cached_raw_position = 0;
uint16_t cached_scaled_position = 0;

#define MOVE_STATUS_OK 0x01
#define MOVE_STATUS_TIMEOUT 0x02
#define MOVE_STATUS_MOVING 0x03
uint8_t last_move_status = MOVE_STATUS_OK;
bool vBAT(bool state);
bool vEXT(bool vext_set_state);
void ensureVBATOn();
void processSlaveStatusResponse(uint8_t blind_number, uint8_t state);
void prepareCommand(uint8_t prep_command, uint8_t blind_number = 0, uint8_t state = 0, uint16_t position = 0, uint16_t real_position = 0, uint8_t last_move_status = 0);
bool loadConfigFromFlash();

bool slave_moving[MAX_SLAVES+1] = {false};

volatile bool configButtonInterruptFlag = false;
volatile bool buttonPressed = false;
volatile unsigned long buttonPressTime = 0;
volatile unsigned long lastInterruptTime = 0;
bool buttonHandled = false;
unsigned long last_slave_poll = 0;
uint8_t last_polled_slave = 1;
unsigned long lastTimeSyncRequest = 0;
bool configPortalActive = false;
unsigned long configPortalStartTime = 0;

Preferences prefs;

// In-memory config
uint32_t config_gatewayID = 0;
uint8_t config_aes_key[16];
uint8_t config_hmacKey[10];
uint32_t config_rf_frequency = 915000000; // Default to AU915 (Australia)
// RTC-persistent list of detected slaves
RTC_DATA_ATTR uint8_t detected_slaves[16] = {0}; // supports up to 15 slaves, 0 = unused
RTC_DATA_ATTR uint8_t detected_slave_count = 0;
unsigned long last_slave_poll_time = 0;
// Provide global access for web_portal.cpp and others
RTC_DATA_ATTR uint16_t slave_positions[16] = {0};

extern uint16_t slave_positions[];
unsigned long vbat_keep_on_until = 0;

bool ledOnWhileAwake = false; // Option to control LED while awake

struct timeval tv_now;
ESP32Time rtc(28800);

/** creating an object of TOTP class */
//TOTP otp = TOTP(config_hmacKey, 10, 1);
TOTP* otp = nullptr;

#define uS_TO_S_FACTOR 1000000 /* Conversion factor for micro seconds to seconds */

/** creating an object of AES128 class */
AES128 aes128;
byte encrypted[16];  //temp storage
byte decrypted[16];  //temp storage

Ewma posEwma(POS_ALPHA);
Ewma battEwma(BATT_ALPHA);

BlindMotorController actuator(
    IN_A_PIN, IN_B_PIN, EN_PIN, EN_PWM_CHANNEL,
    POSITION_PIN, POSITION_REF_PIN
);

/** LoRa callback events */
static RadioEvents_t RadioEvents;

/** HW configuration structure for the LoRa library */
hw_config hwConfig;

// Event declarations
void OnTxDone(void);
void OnRxDone(uint8_t *payload, uint16_t size, int16_t rssi, int8_t snr);
void OnTxTimeout(void);
void OnRxTimeout(void);
void OnRxError(void);
void OnCadDone(bool cadResult);

// flag once full init done to be able to tx
bool fullInit = false;

/** The encoded part of the message */
// order of OTP 3bytes and command prior to 32bit node id, allows 4 extra bytes of payload while still being 16bytes for aes128
struct dataPacket {
  uint8_t OTP[3];
  uint8_t command;
  uint32_t nodeFROMId;
  uint8_t payload[8];
} dataToENC, dataDEC;

/** The Data message will be sent by the node */
struct loraPacket {
  uint32_t nodeToId;
  uint8_t dataEncrypted[16];
} loraTXpacket, prevloraRXpacket, tmploraRXpacket;

namespace data {
typedef struct {
  uint32_t nodeToId;
  uint8_t dataEncrypted[16];
} loraRXpacket;
}

CircularBuffer<data::loraRXpacket, 10> loraRXbuffer;

struct commandPacket {
  uint8_t command;
  uint8_t payload[8];
} command, commandTX;

/** The sensor node ID, created from MAC of ESP32 */
uint32_t deviceID;

/** LoRa error timeout */
time_t loraTimeout;

/** LoRa TX time */
time_t loraTXTime;

/** CAD repeat counter */
uint8_t cadRepeat;

bool commandReady = false;

bool txComplete = true;

int buff_size = 0;

/** The wakeup time */
time_t wakeup;
time_t start_enc;
time_t position_updated;
time_t status_update;
time_t slave_status_update;

time_t motor_start_time;
time_t motor_run_time;

uint16_t targetPos;  // position in % x 10
uint8_t blind_state = STATE_UNKNOWN;

bool vext_state = false;
bool vbat_state = false;

bool slave_reading = false;

RTC_DATA_ATTR uint16_t wakeCount;
RTC_DATA_ATTR time_t awakeTime;
RTC_DATA_ATTR time_t lastSend;
RTC_DATA_ATTR time_t lastTimeSync;  //records the last time the timeSync was performed for rate limiting
RTC_DATA_ATTR int timeSync;  //records if we are currently performing a time sync, and counts number of attempts
RTC_DATA_ATTR uint32_t timeNow;  //saved so it can sleep when waiting for timesync
#ifdef SIMULATOR
RTC_DATA_ATTR int posSIM = 0;
#endif

bool msgInBuffer = false; // Flag to indicate if a message is in the RX buffer when performing a time sync



bool configMode = false;

// Buffer for uploaded config file
String uploadedConfigFile;

/** declare functions */
void setVBATKeepOn(unsigned long duration_ms);
void goToSleep(void);
void radioSetup(void);
void radioInit(void);
uint8_t checkOTP(uint8_t OTP[3]);
void buildPacket(uint32_t toNodeID, time_t OTPtime, commandPacket commandToSend);
void actionCommand(void);
void parsePacket(void);
void performTimeSync(void);
uint16_t checkBAT(void);
void print_reset_reason(RESET_REASON reason);
void startConfigAPAndWebserver();
void stopConfigAPAndWebserver();
void scanUARTSlavesAndPublish();
const char* getMoveStatusString(uint8_t status);
void handleSetClosedLimit(AsyncWebServerRequest *request);
void handleSetOpenLimit(AsyncWebServerRequest *request);
void handleGetPosition(AsyncWebServerRequest *request);
void updateVBATState();
bool isConfigMissing() {
  return !loadConfigFromFlash();
}
bool any_slave_moving() {
  for (uint8_t i = 1; i <= MAX_SLAVES; ++i) {
      if (slave_moving[i]) return true;
  }
  return false;
}
void loadTimingSettingsFromFlash();
void handleAutoCalibrate(AsyncWebServerRequest *request);

// Helper: hex string to bytes
bool hexToBytes(const char* hex, uint8_t* buf, size_t len) {
for (size_t i = 0; i < len; ++i) {
  char tmp[3] = {hex[i*2], hex[i*2+1], 0};
  char* endptr;
  long val = strtol(tmp, &endptr, 16);
  if (*endptr != 0) return false;
  buf[i] = (uint8_t)val;
}
return true;
}

// CRC-16-CCITT
uint16_t crc16_ccitt(const uint8_t* data, size_t len) {
  uint16_t crc = 0xFFFF;
  for (size_t i = 0; i < len; i++) {
      crc ^= (uint16_t)data[i] << 8;
      for (uint8_t j = 0; j < 8; j++)
          crc = (crc & 0x8000) ? (crc << 1) ^ 0x1021 : (crc << 1);
  }
  return crc;
}


// Send UART frame to slave
bool sendUARTCommandToSlave(uint8_t slave_addr, uint8_t command, uint8_t *payload) {
  RS485_TRANSMIT();
  delayMicroseconds(10); // Allow line to settle
  uint8_t frame[1 + 1 + 1 + 8 + 2 + 1];
  size_t idx = 0;
  frame[idx++] = UART_START_BYTE;
  frame[idx++] = slave_addr;
  frame[idx++] = command;
  for (int i = 0; i < 8; ++i) frame[idx++] = payload ? payload[i] : 0;
  uint16_t crc = crc16_ccitt(&frame[1], 1 + 1 + 8); // addr+cmd+payload
  frame[idx++] = (crc >> 8) & 0xFF;
  frame[idx++] = crc & 0xFF;
  frame[idx++] = UART_END_BYTE;
  Serial1.write(frame, sizeof(frame));
  Serial1.flush();
  delayMicroseconds(5); // Allow last byte to leave the bus
  RS485_RECEIVE();
  return true;
}

// Receive UART frame from slave (blocking, with timeout)
bool receiveUARTResponse(uint8_t expected_addr, uint8_t *command, uint8_t *payload, uint32_t timeout_ms = UART_TIMEOUT_MS) {
  uint8_t buf[1 + 1 + 1 + 8 + 2 + 1];
  size_t idx = 0;
  unsigned long start = millis();
  while (millis() - start < timeout_ms) {
      if (Serial1.available()) {
          uint8_t b = Serial1.read();
          if (idx == 0 && b != UART_START_BYTE) {
              LOG_DEBUG("[UART RX] Skipping byte 0x%02X (waiting for start byte)\r\n", b);
              continue;
          }
          buf[idx++] = b;
          LOG_DEBUG("[UART RX] Received byte: 0x%02X (idx=%d)\r\n", b, idx-1);
          if (idx == sizeof(buf)) {
              LOG_DEBUG("[UART RX] Full frame received: ");
              for (size_t i = 0; i < sizeof(buf); ++i) LOG_DEBUG_RAW("%02X ", buf[i]);
              LOG_DEBUG_RAW("\r\n");
              if (buf[0] != UART_START_BYTE || buf[13] != UART_END_BYTE) {
                  LOG_ERROR("[UART RX] Invalid frame: start=0x%02X end=0x%02X\r\n", buf[0], buf[13]);
                  return false;
              }
              if (buf[1] != expected_addr) {
                  LOG_ERROR("[UART RX] Address mismatch: got 0x%02X, expected 0x%02X\r\n", buf[1], expected_addr);
                  return false;
              }
              uint16_t crc = (buf[11] << 8) | buf[12];
              uint16_t calc_crc = crc16_ccitt(&buf[1], 1 + 1 + 8);
              if (calc_crc != crc) {
                  LOG_ERROR("[UART RX] CRC mismatch: received=0x%04X calculated=0x%04X\r\n", crc, calc_crc);
                  return false;
              }
              LOG_INFO("[UART RX] Frame valid!\r\n");
              *command = buf[2];
              for (int i = 0; i < 8; ++i) payload[i] = buf[3 + i];
              return true;
          }
      }
  }
  LOG_WARN("[UART RX] Timeout waiting for response\r\n");
  if (idx > 0) {
      LOG_WARN("[UART RX] Partial frame: ");
      for (size_t i = 0; i < idx; ++i) LOG_WARN("%02X ", buf[i]);
      LOG_WARN("\r\n");
  }
  return false;
}

void processSlaveStatusResponse(uint8_t blind_number, uint8_t state) {
  if (blind_number > 0 && blind_number <= MAX_SLAVES) {
      bool was_moving = slave_moving[blind_number];
      if (state == STATE_OPENING || state == STATE_CLOSING) {
          slave_moving[blind_number] = true;
      } else {
          slave_moving[blind_number] = false;
          // If the slave was moving and now stopped, keep vBAT on for disengage_time
          if (was_moving) {
              setVBATKeepOn(2000);
          }
      }
  }
}
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
void loop() {
    Radio.IrqProcess(); // Process radio interrupts first
    handleConfigButton();

    if (commandReady) {
        actionCommand();
    }

    // there is something in the buffer and (if timesync requested wait for additional packet)
    if (!loraRXbuffer.isEmpty() && !(timeSync > 0 && buff_size == loraRXbuffer.size())) {
        parsePacket();
    }
    static BlindMotorState lastState = BlindMotorState::IDLE;
    BlindMotorState currentState = actuator.getState();
    if ((lastState == BlindMotorState::MOVING || lastState == BlindMotorState::DISENGAGING) &&
        currentState == BlindMotorState::IDLE) {
        // Move just finished, send final status update
        actuator.reportStatus();
        prepareCommand(BLIND_STATUS, 0, actuator.getCoverState(), actuator.readPositionPercent(), actuator.readPositionRaw(), actuator.getLastMoveStatus());
    }
    lastState = currentState;

    if (actuator.isMotorRunning()) {
      if (millis() - status_update > MOVING_UPDATE_PERIOD) {
        status_update = millis();
        actuator.reportStatus();
        prepareCommand(BLIND_STATUS, 0, actuator.getCoverState(), actuator.readPositionPercent(), actuator.readPositionPercent(), actuator.getLastMoveStatus());
      }
    }
    if (any_slave_moving()) {
      if (millis() - slave_status_update > MOVING_UPDATE_PERIOD) {
        slave_status_update = millis();
        for (uint8_t i = 0; i < detected_slave_count; ++i) {
          uint8_t blind_number = detected_slaves[i];
          if (slave_moving[blind_number]) {
            pollSlaveStatusUART(blind_number);
          }
        }
      }
    }
    if (configPortalActive && millis() - configPortalStartTime > 10 * 60 * 1000) {
        stopConfigAPAndWebserver(); // Your function to stop the web portal
        configPortalActive = false;
    }
    if (millis() - wakeup > MAX_AWAKE_TIME) {
        LOG_WARN("10min timeout\r\n");
        timeSync = 0;
        lastTimeSync = 0;
        goToSleep();
    }

    // Check for LoRa timeout - tx command didnt finish within 20 seconds
    if ((millis() - loraTimeout) > LORA_TIMEOUT && (!txComplete || timeSync > 0)) {
        LOG_WARN("LoRa loop timeout\r\n");
        // LoRa failed, go back to bed
        timeSync = 0;
        lastTimeSync = 0;
        goToSleep();
    }

    // Perform time sync if its not set already. and send periodic updates
    if (loraRXbuffer.isEmpty() && !commandReady && txComplete && !(timeSync > 0) && millis() > 90) {
        gettimeofday(&tv_now, NULL);
        int32_t time = (int32_t)tv_now.tv_sec;
        if (time < 60000000) {  //its not set, but could be second run
          if(time < 15000000) { //its first run since boot, give a random seed for otp
            tv_now.tv_sec = random(15000001, 30000000);
            settimeofday(&tv_now, NULL);
          }
            if (!(lastTimeSync == 0) && time - lastTimeSync < TIME_SYNC_RATE_LIMIT) {
                //its failed recently
            } else {
                performTimeSync();
                return;
            }
        }

        if (time - lastSend > UPDATE_PERIOD && timeSync == 0) {
            lastSend = time;
            slave_reading = true;
            prepareCommand(DEVICE_STATUS);
            prepareCommand(BLIND_STATUS, 0, actuator.getCoverState(), actuator.readPositionPercent(), actuator.readPositionPercent(), actuator.getLastMoveStatus());

            if (detected_slave_count > 0) ensureVBATOn();
            for (uint8_t i = 0; i < detected_slave_count; ++i) {
              pollSlaveStatusUART(detected_slaves[i]);
            }
            slave_reading = false;
            updateVBATState();
            return;
        }
        if (configPortalActive == true || actuator.isMotorRunning() || any_slave_moving() || slave_reading) {
            // If config portal is active, don't go to sleep
            return;
        }
        if (millis() < vbat_keep_on_until) {
          return;
        }
        // nothing left to do..

        goToSleep();
    }
    updateVBATState();
}

void ensureVBATOn() {
  if (!vbat_state) {
      vBAT(true);
      vEXT(true); // Ensure logic shifter is on for RS485
      delay(VBAT_BOOT_MS);
  } else if (!vext_state) {
      vEXT(true); // If vBAT is already on, still ensure vEXT is on
  }
}

void setVBATKeepOn(unsigned long duration_ms) {
  ensureVBATOn();
  unsigned long new_until = millis() + duration_ms;
  if (new_until > vbat_keep_on_until) vbat_keep_on_until = new_until;
}

void updateVBATState() {
  if (!actuator.isMotorRunning() && !any_slave_moving() && !slave_reading && millis() > vbat_keep_on_until) {
      vBAT(false);
  } 
}
// function to enable the mosfet on the battery, normally used for reading battery voltage, but hacked to power the motor driver board with battery voltage not the regulated power.
bool vBAT(bool state) {
  if (state && !vbat_state) {
    // requested on, but current state is off
    digitalWrite(BATTERY_PIN, LOW);
    vbat_state = true;
    LOG_INFO("vBAT Enabled\r\n");
    delay(10);
    return true;
  }
  if (!state && vbat_state && !actuator.isMotorRunning() && !any_slave_moving() && !slave_reading) {  //make sure motor is not running before turning off
    digitalWrite(BATTERY_PIN, HIGH);
    vbat_state = false;
    LOG_INFO("vBAT Disabled\r\n");
    return false;
  }
  return state;
}

uint16_t checkBAT(void) {
  ensureVBATOn();
  int battRaw = analogReadMilliVolts(BATTERY_ADC_PIN);
  int battAvg = battEwma.filter(battRaw);
  uint16_t battCalc = battAvg * 4.900;  // based on 390k and 100k voltage divider

  LOG_INFO("avg voltage at GPIO 01: %d  Battery voltage: %d\r\n", battRaw, battCalc);
  updateVBATState();
  return battCalc;
}

// function to enable the 2nd voltage regulator, used for position sensor and rs485 module
bool vEXT(bool vext_set_state) {
  if (vext_set_state && !vext_state) {
    // requested on, but current state is off
    digitalWrite(VEXT_PIN, LOW);
    vext_state = true;
    LOG_INFO("vEXT Enabled\r\n");
    delay(500);
    return true;
  }
  if (!vext_set_state && vext_state) {
    digitalWrite(VEXT_PIN, HIGH);
    vext_state = false;
    LOG_INFO("vEXT Disabled\r\n");
    return false;
  }
  return vext_set_state;
}

uint8_t checkOTP(uint8_t OTP[3]) {
  
  gettimeofday(&tv_now, NULL);
  int64_t time = (int64_t)tv_now.tv_sec;
  uint32_t intCode = OTP[0] | (OTP[1] << 8) | (OTP[2] << 16);
  if (timeSync > 0) {  //could be using random time set in timeNow, otherwise otp may be predictable when rtc is 0
    if (intCode == (uint32_t)atoi(otp->getCode(timeNow))) return 0xBB;
  }
  for (uint8_t idx = 0; idx < OTP_RANGE; idx++) {
    if (intCode == (uint32_t)atoi(otp->getCode(time + idx))) return idx + 1;
    if (intCode == (uint32_t)atoi(otp->getCode(time - idx))) return (idx + 1) << 4;
  }
  return 0x00;
}
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

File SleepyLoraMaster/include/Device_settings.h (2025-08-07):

// SPDX-License-Identifier: MIT
// Copyright (c) 2025 Chris Huitema

#define TIME_TO_SLEEP  60      // Time ESP32 will go to sleep (in seconds).
#define MAX_AWAKE_TIME 600000   // max time the device can be awake
#define UPDATE_PERIOD 60        // how often to send updates
#define OTP_RANGE 5             // max time difference allowed for valid OTP 
#define MOVING_UPDATE_PERIOD 1500

#define POS_ALPHA 0.7
#define BATT_ALPHA 0.7
#define EN_PWM_CHANNEL 0 // PWM channel for enable pin

#define VBAT_BOOT_MS 1800   // Time to allow slaves to boot up before communicating with them

#define BATTERY_PIN 37
#define BATTERY_ADC_PIN 01
#define VEXT_PIN 36
#define LED_PIN 35
#define POSITION_PIN 7
#define POSITION_REF_PIN 15 // GPIO15: Pot top (reference)
#define IN_A_PIN 17 //
#define IN_B_PIN 18 //
#define EN_PIN 4

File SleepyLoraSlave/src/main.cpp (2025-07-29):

// SPDX-License-Identifier: MIT
// Copyright (c) 2025 Chris Huitema

// SleepyLoRaSlave blind controller firmware. receives commands via RS485 UART from master controller.
// The master controller is responsible for managing the LoRa communication and sending commands to this slave device.
// This slave device controls a blind motor and reports its position and state back to the master controller.
// The slave device can also be configured via a web portal to change its RS485 address and other settings.
// The device can be updated OTA via the web portal.


#include <Arduino.h>
#include <Ewma.h>
#include <Preferences.h>
#include <WiFi.h>
#include <AsyncTCP.h>
#include <ESPAsyncWebServer.h>
#include <Update.h>
#include <Ticker.h>
#include <nvs_flash.h>
#include <AsyncEventSource.h>
#include <algorithm> // For std::min and std::max

#include "Command_Register.h"
#include "BlindMotorController.h"
#include "web_portal.h"


// Debug macros with log levels
#define DEBUG_SERIAL

#define LOG_LEVEL_ERROR   1
#define LOG_LEVEL_WARN    2
#define LOG_LEVEL_INFO    3
#define LOG_LEVEL_DEBUG   4

#ifndef DEBUG_LEVEL
#define DEBUG_LEVEL LOG_LEVEL_DEBUG  // Set default log level here
#endif

#ifdef DEBUG_SERIAL
  #define LOG_ERROR(...)   do { if (DEBUG_LEVEL >= LOG_LEVEL_ERROR) Serial.printf("[ERROR] " __VA_ARGS__); } while(0)
  #define LOG_WARN(...)    do { if (DEBUG_LEVEL >= LOG_LEVEL_WARN)  Serial.printf("[WARN] "  __VA_ARGS__); } while(0)
  #define LOG_INFO(...)    do { if (DEBUG_LEVEL >= LOG_LEVEL_INFO)  Serial.printf("[INFO] "  __VA_ARGS__); } while(0)
  #define LOG_DEBUG(...)   do { if (DEBUG_LEVEL >= LOG_LEVEL_DEBUG) Serial.printf("[DEBUG] " __VA_ARGS__); } while(0)
  #define LOG_DEBUG_RAW(...) do { if (DEBUG_LEVEL >= LOG_LEVEL_DEBUG) Serial.printf(__VA_ARGS__); } while(0)
#else
  #define LOG_ERROR(...)
  #define LOG_WARN(...)
  #define LOG_INFO(...)
  #define LOG_DEBUG(...)
  #define LOG_DEBUG_RAW(...)
#endif

// Pin definitions
#define POSITION_PIN 4
#define IN_A_PIN 10
#define IN_B_PIN 20
#define EN_PIN 7
#define EN_PWM_CHANNEL 0 // PWM channel for enable pin
#define POSITION_REF_PIN 3 // GPIO3: Pot top (reference)

// RS485 direction control pin for slave
#define RS485_DIR_PIN 8
#define RS485_TRANSMIT()  digitalWrite(RS485_DIR_PIN, HIGH)
#define RS485_RECEIVE()   digitalWrite(RS485_DIR_PIN, LOW)

// UART protocol constants
#define UART_START_BYTE 0xAA
#define UART_END_BYTE   0x55
#define UART_BAUDRATE   115200
#define UART_TX_PIN     6
#define UART_RX_PIN     5
uint8_t slave_number = 1; // default

uint8_t rs485_addr = 0x20; // Default address, can be changed via web portal

// Command codes (should match master's Command_Register.h)
#define BLIND_COMMAND 0x03
#define GET_STATUS    0x08
#define UPDATE_SLAVE 0x09


// State definitions (should match master's enum)
#define STATE_CLOSING  0x01
#define STATE_OPENING  0x02
#define STATE_CLOSED   0x03
#define STATE_OPEN     0x04

//dummy definitions for web portal library
uint32_t config_gatewayID = 0;
uint8_t config_aes_key[16] = {0};
uint8_t config_hmacKey[10] = {0};
uint32_t config_rf_frequency = 868100000;
bool configMode = false;
void saveConfigToFlash() {}
bool hexToBytes(const char*, uint8_t*, size_t) { return false; }
void scanUARTSlavesAndPublish() {}
bool sendCommandToSlaveUART(uint8_t, uint8_t, uint8_t*, size_t) { return false; }
uint8_t detected_slaves[1] = {0};
uint8_t detected_slave_count = 0;
uint16_t slave_positions[1] = {0};
bool slave_moving[1] = {false};
uint32_t deviceID = 0;


volatile uint8_t last_command = 0;
volatile uint8_t last_payload[8];
volatile bool command_received = false;

bool configPortalActive = false;
unsigned long configPortalStartTime = 0;

Preferences prefs;

BlindMotorController actuator(
    IN_A_PIN, IN_B_PIN, EN_PIN, EN_PWM_CHANNEL,
    POSITION_PIN, POSITION_REF_PIN
);

uint16_t targetPos;  // position in % x 10
uint8_t blind_state = STATE_UNKNOWN;

uint16_t blind_position = 0;

bool isAddressInUse(uint8_t candidate_addr);

// CRC-16-CCITT
uint16_t crc16_ccitt(const uint8_t* data, size_t len) {
    uint16_t crc = 0xFFFF;
    for (size_t i = 0; i < len; i++) {
        crc ^= (uint16_t)data[i] << 8;
        for (uint8_t j = 0; j < 8; j++)
            crc = (crc & 0x8000) ? (crc << 1) ^ 0x1021 : (crc << 1);
    }
    return crc;
}

void sendUARTResponse(uint8_t command, uint8_t *payload) {
    delayMicroseconds(10); 
    RS485_TRANSMIT();
    delayMicroseconds(20); // Allow line to settle
    uint8_t frame[1 + 1 + 1 + 8 + 2 + 1];
    size_t idx = 0;
    frame[idx++] = UART_START_BYTE;
    frame[idx++] = rs485_addr;
    frame[idx++] = command;
    for (int i = 0; i < 8; ++i) frame[idx++] = payload ? payload[i] : 0;
    uint16_t crc = crc16_ccitt(&frame[1], 1 + 1 + 8);
    frame[idx++] = (crc >> 8) & 0xFF;
    frame[idx++] = crc & 0xFF;
    frame[idx++] = UART_END_BYTE;
    LOG_DEBUG("[UART TX] Raw frame: \r\n");
    for (size_t i = 0; i < sizeof(frame); ++i) LOG_DEBUG_RAW("%02X ", frame[i]);
    LOG_DEBUG_RAW("\r\n");
    Serial1.write(frame, sizeof(frame));
    Serial1.flush();
    delayMicroseconds(30); // Allow last byte to leave the bus
    RS485_RECEIVE();
}

void eraseNVSAndReboot() {
    LOG_ERROR("[NVS] Erasing NVS partition and rebooting...\n");
    nvs_flash_erase();
    nvs_flash_init();
    delay(100);
    ESP.restart();
}
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

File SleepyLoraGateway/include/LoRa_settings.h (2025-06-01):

// SPDX-License-Identifier: MIT
// Copyright (c) 2025 Chris Huitema

// Heltec - SX126x pin configuration
int PIN_LORA_RESET = 12;
int PIN_LORA_BUSY = 13;
int PIN_LORA_DIO_1 = 14;
int PIN_LORA_NSS = 8;
int PIN_LORA_SCLK = 9;
int PIN_LORA_MISO = 11;
int PIN_LORA_MOSI = 10;
int RADIO_TXEN = -1;
int RADIO_RXEN = -1;

/** Number of retries if CAD shows busy */
#define CAD_RETRY 20
#define LORA_TIMEOUT 20000

// Define LoRa parameters
// #define RF_FREQUENCY 915000000 // Hz
// Use config.rf_frequency instead of hardcoded define
#define TX_OUTPUT_POWER 22      // dBm
#define LORA_BANDWIDTH 0        // [0: 125 kHz, 1: 250 kHz, 2: 500 kHz, 3: Reserved]
#define LORA_SPREADING_FACTOR 7 // [SF7..SF12]
#define LORA_CODINGRATE 1       // [1: 4/5, 2: 4/6,  3: 4/7,  4: 4/8]
#define LORA_PREAMBLE_LENGTH 8 // Increased for Blinds: 60ms sleep + 30ms Rx + buffer
#define LORA_SYMBOL_TIMEOUT 0   // Symbols
#define LORA_FIX_LENGTH_PAYLOAD_ON false
#define LORA_IQ_INVERSION_ON false
#define RX_TIMEOUT_VALUE 3000
#define TX_TIMEOUT_VALUE 3000

#define BUFFER_SIZE 512 // Define the payload size here

#define TIME_SYNC_RETRIES 3
#define TIME_SYNC_RATE_LIMIT 5  //s  timeout after setting clock

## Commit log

2025-06-01 Initial Upload of files
    [BOM.CSV, BOM.csv, Blind_SleepyLoRa.kicad_pcb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]
2025-06-01 Initial commit of Actuator device firmware
2025-06-04 Try and prevent log corruption. general code tidy up. improve OTP time stability by ensuring time used is as close to packet send time as possible
    [logger.cpp, main.cpp, webserver.cpp]
2025-06-05 Added missing screws for link bar cplamps to BOM
    [BOM.CSV]
2025-06-05 Added reversed actuator cam for use when actuator is on the right hand side of the plantation shutter. Actuator will be extended when closed and retracted when open, which is reverse of the left hand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
2025-06-06 corrected MQTT keepalive to 15sec
    [main.cpp]
2025-06-07 adding pre-supported print files. chitubox file comepressed due to size limit
2025-06-07 Add print instructions
2025-06-10 Add links to assembly videos
2025-06-11 Correct pin assignment for V2 Master PCB.
    [main.cpp]
2025-06-11 Improved logging and fix TX buffer filling while waiting for ack issue
    [logger.cpp, main.cpp, mqtt.cpp]
2025-06-11 Add EN pin to slave device for new V2 PCB. Change from echo of received command to reply with status update
2025-06-11 Added buttons to webserver to set closed and open positions, values are saved to flash and loaded on boot.
2025-06-11 Add Open and Closed Calibration to MAster
2025-06-14 Add reference voltage to make position more accurate when motor running.
2025-06-15 Update master PCB to include ref voltage
    [Blind_SleepyLoRa.kicad_pcb, Blind_SleepyLoRa.kicad_sch]
2025-06-16 squash silly bug. ensure full rx buffer is processed before resending unack packet
    [main.cpp]
2025-06-20 Add PWM speed control and improve nvs error handling.
    [main.cpp]
2025-06-21 Add calibration routine. improve position filter.
2025-06-23 significant changes, added dynamic PWM to set a target stroke time
2025-09-30 Config portal closing instantly fix.
    [main.cpp]
